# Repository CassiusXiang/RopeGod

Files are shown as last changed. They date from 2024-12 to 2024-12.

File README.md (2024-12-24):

# RopeGod



## Introduction
RopeGod is a highly integrated and low-cost rope-driven five-finger dexterous hand with a total of 7 degrees of freedom.

Each finger segment is equipped with 2 pressure sensors, making a total of 11 force sensors.

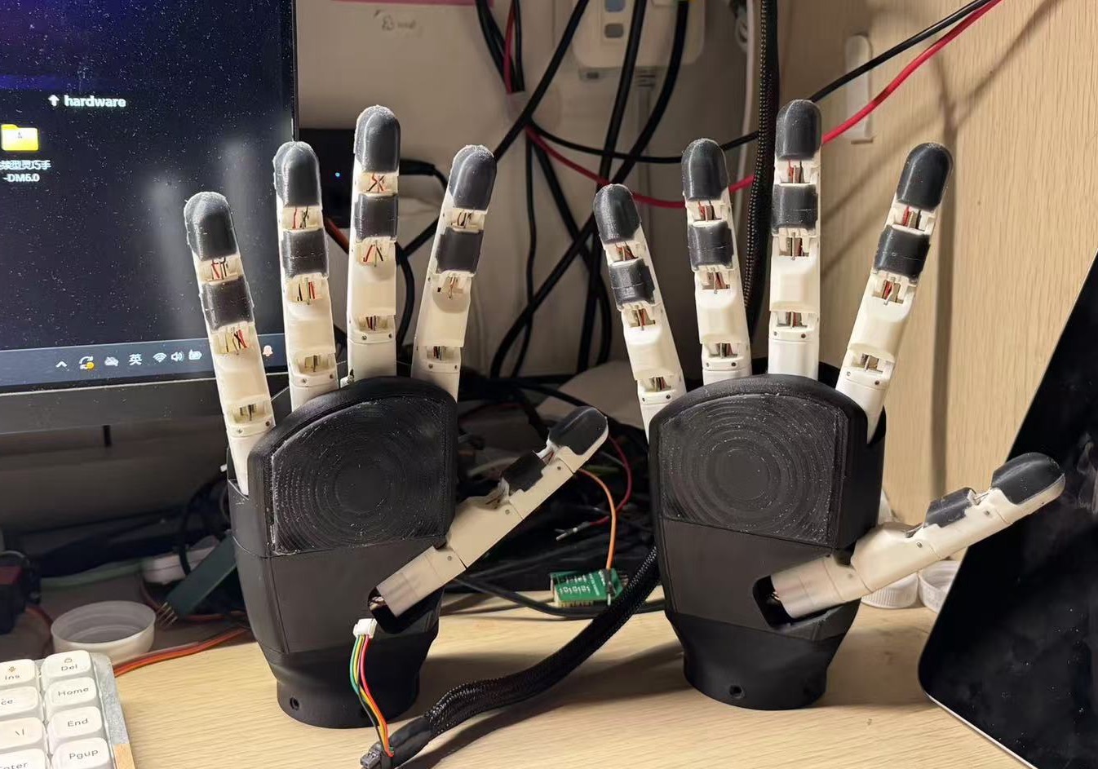
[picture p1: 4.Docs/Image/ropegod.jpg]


## Performance Parameters

| Parameter | Value |
|---|---|
| Weight | 346g |
| Cost | <60$ |
| Number of Sensors | 11 |
| Degrees of Freedom | 7 |
| Maximum Single-Finger Downward Force | 8N |
| Maximum Lifting Weight | 2Kg |
| Power Supply Voltage | 12 ~ 24V |
| Maximum Current | 1.5A |
| Communication | CAN |

## Mechanical Structure

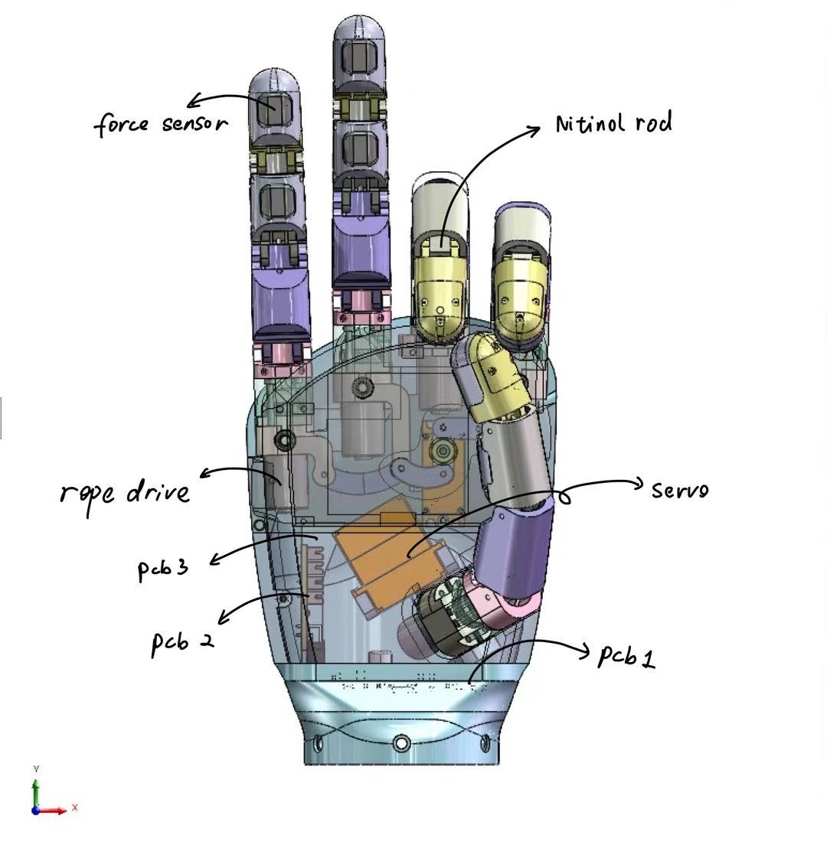
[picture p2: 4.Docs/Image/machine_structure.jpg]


Except for the servos and coreless motors, all other components are independently designed. They can be manufactured via 3D printing, silicone molding with 3D-printed molds, and basic mechanical processing. The models can be found in `/0.Model`.

Currently, our drive structure still involves a single driver board controlling multiple degrees of freedom. Going forward, we are shifting toward a modular design for individual fingers, aiming to integrate drive, control, and current feedback into a single finger, with inter-finger connections using a bus for communication. This will further enhance modular design and reduce space and resource waste.

## Circuit Design

There are three circuit boards inside the palm:
- Motor driver board
- Expansion board (provides driver interfaces)
- Sensor sampling board

This distributed circuit design can further reduce space usage and improve integration. It also offers high flexibility. For example, by changing the sensor board, you can adapt to various sensors (e.g., visual-tactile sensors).

The main control board uses the STM32F103C8T6 for motor control. Each finger’s coreless motor comes with a resistance-based encoder and a closed-loop control board. Therefore, the main controller only needs to supply a stable 12V and an accurate PWM signal to control the rope-driven actuators similarly to controlling servos.

The sensor board uses the STM32F103VET6 as the main controller, primarily because it offers more ADC channels compared to smaller-packaged STM32F1 versions.

Refer to `/1.Hardware` for schematics and PCB designs.

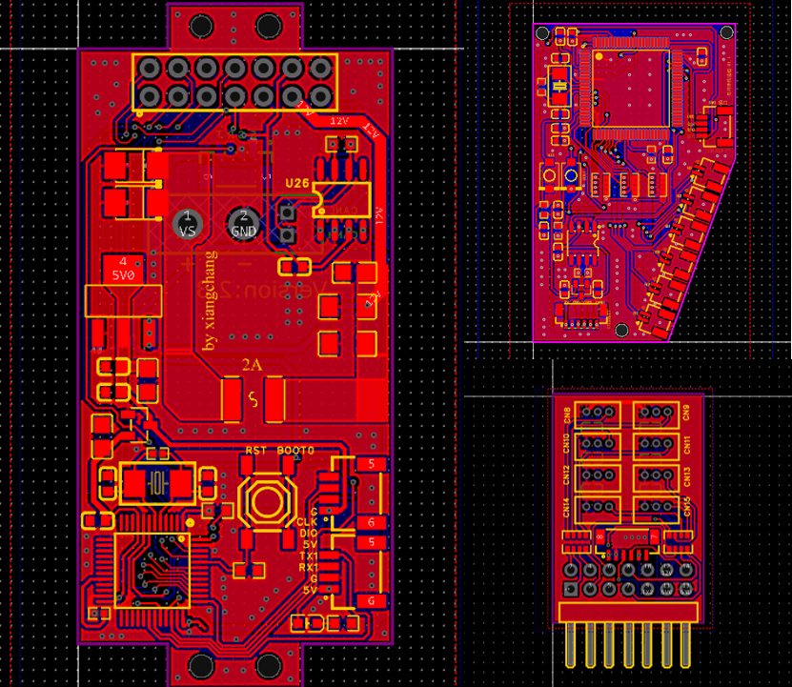
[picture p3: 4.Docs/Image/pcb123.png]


## Firmware

Both the main control board and the sensor board are developed using STM32CubeIDE.

Source code can be found in `2.Firmware`.

## Communication

Since the STM32 series is equipped with a CAN controller peripheral, we only need to add a TJA1042 transceiver. This has already been configured on both the main control board and the sensor board, and both are connected to the CAN network.

For details on the communication protocol, see: [Communication Protocol](./4.Docs/)

## Upper Computer (Host Software)

We use QT to develop a host software application for convenient operation and data collection.

Currently supported features:
1. Closed-loop position control of 7 degrees of freedom
2. Serial connection to a USB-CAN controller
3. Display of joint angle parameters
4. Execution of 4 basic actions (pinch, spherical grasp, lateral pinch, cylindrical grasp)
5. Setting the CAN IDs of the dexterous hand and sensors
6. Chart display of 12 pressure sensor readings

The source code of the upper computer software can be found in `./3.Software`. A pre-compiled version is published in the release section (currently only Windows).

Support for high-resolution screens is not ideal at the moment. We plan to fix this in subsequent releases.

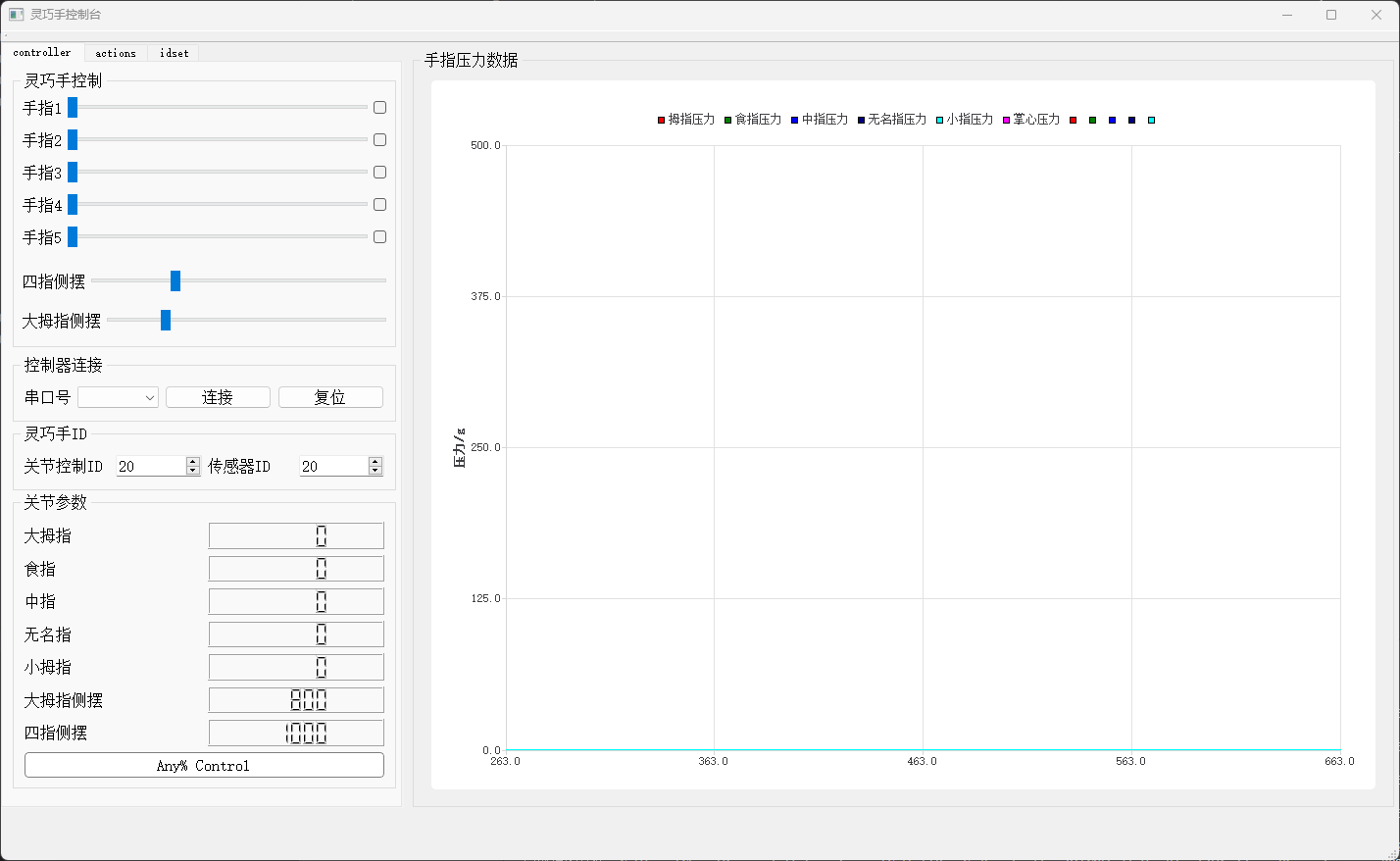
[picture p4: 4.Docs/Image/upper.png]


## Libraries and Interfaces

We provide both C++ and Python library interfaces for convenient secondary development.

See `./3.Software` for details.

Creating a dexterous hand object in C++:
```cpp
WzSerialPort w;
mrh5 mr1(w, 32, 33); 
```

The control frequency should be <200 Hz.

## Video Demonstration
- Degrees of freedom demo: Link 1
- Automatically grasping 9 types of objects and using a barcode scanner to scan barcodes: Link 2
- Using a continuum dexterous hand to grasp fragile items like chips and eggs: Link 3

## Derivative Projects
- Continuum Dexterous Hand
- Metamorphic Dexterous Hand

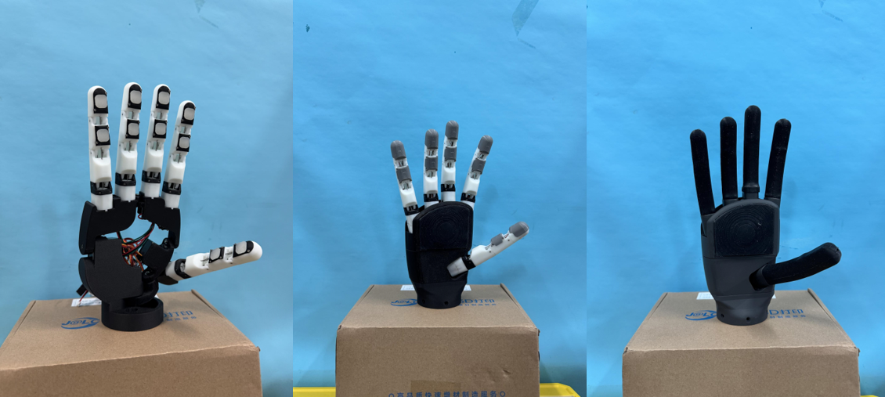
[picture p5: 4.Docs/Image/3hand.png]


## License
Choloepus is released under the AGPL-3.0 License. Please refer to [LICENSE](https://github.com/CassiusXiang/Choloepus/blob/main/LICENSE) for more information.

## Contact
Email: changxiangchina@outlook.com

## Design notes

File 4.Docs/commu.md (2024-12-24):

## Communication Protocol

[go Back](../README.md)

First, connect the USB-CAN module to the computer.

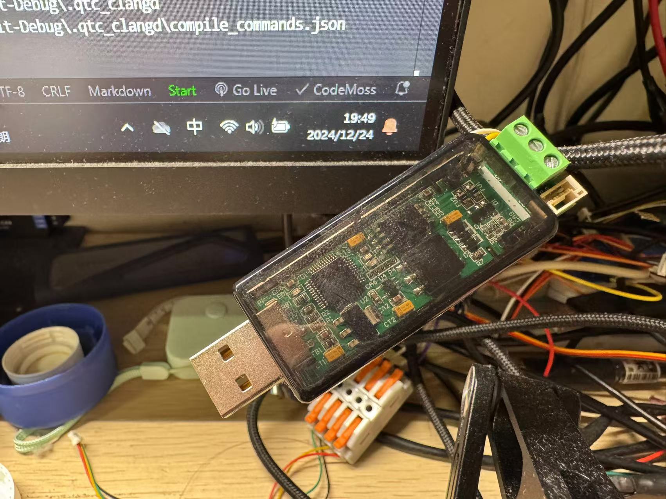
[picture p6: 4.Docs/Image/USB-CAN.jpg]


## Setting Servo Angle

The serial command for setting the servo angle is 16 bytes in length, detailed as follows:

| Command Index | Hex Value |
|---|---|
| 0 | AA |
| 1 | 00 |
| 2 | 00 |
| 3 | 08 |
| 4 | 00 |
| 5 | 00 |
| 6 | High byte of ID |
| 7 | Low byte of ID |
| 8 | 01 |
| 9 | Servo Number |
| 10 | High byte of Angle|
| 11 | Low byte of Angle |
| 12 | 00 |
| 13 | 00 |
| 14 | 00 |
| 15 | 00 |

Angle Correspondence: The physical servo angle ranges from 0 to 180 degrees, corresponding to an electrical servo angle ranging from 0 to 2000.

## Pressure Reading

The pressure data format returned by the sensor is as follows:

The sensor ID is calculated as 2047 minus the set sensor ID (default is 33).

| Command Index | Hex Value |
|---|---|
| 0 | AA |
| 1 | 00 |
| 2 | 00 |
| 3 | 08 |
| 4 | 00 |
| 5 | 00 |
| 6 | High byte of ID |
| 7 | Low byte of ID |
| 8 | Pressure Sensor Number |
| 9 | High byte of Pressure Data |
| 10 | Low byte of Pressure Data  |
| 11 | 00 |
| 12 | 00 |
| 13 | 00 |
| 14 | 00 |
| 15 | 00 |

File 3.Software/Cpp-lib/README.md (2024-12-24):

# MRH5 灵巧手C++库

本项目适用于Windows平台

在根目录下，运行：

```\
make
```

即可生成可执行文件

如果您未经设置可能不能直接使用make，可以用如下命令代替

```
mingw32-make.exe
```

## 备注

- 在Windows上，要打开COM10以后的串口（包括COM10），串口名称不再是“COM10”，而是“\\.\COM10”，因此在open函数中，如果是COM10及以后的串口，串口名（假设当前要打开COM10）应该写“\\\\.\\COM10”，其中“\\\\.\\”为“\\.\”的转义。

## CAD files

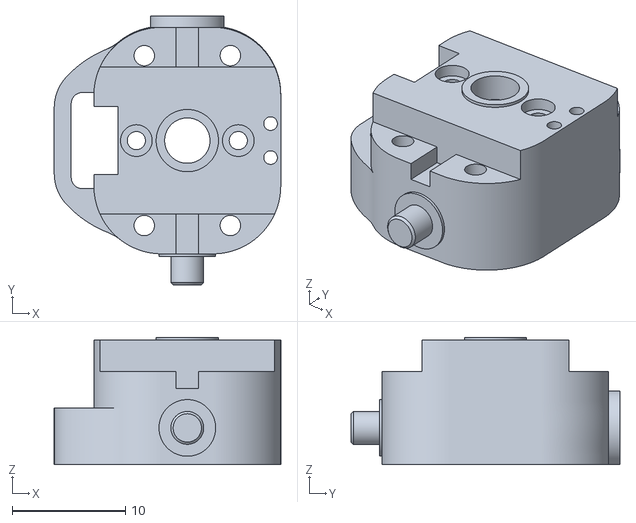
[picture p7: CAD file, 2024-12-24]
0.Model/三维猴打印/拇指机架_L.STL
20.0 x 23.8 x 11.2

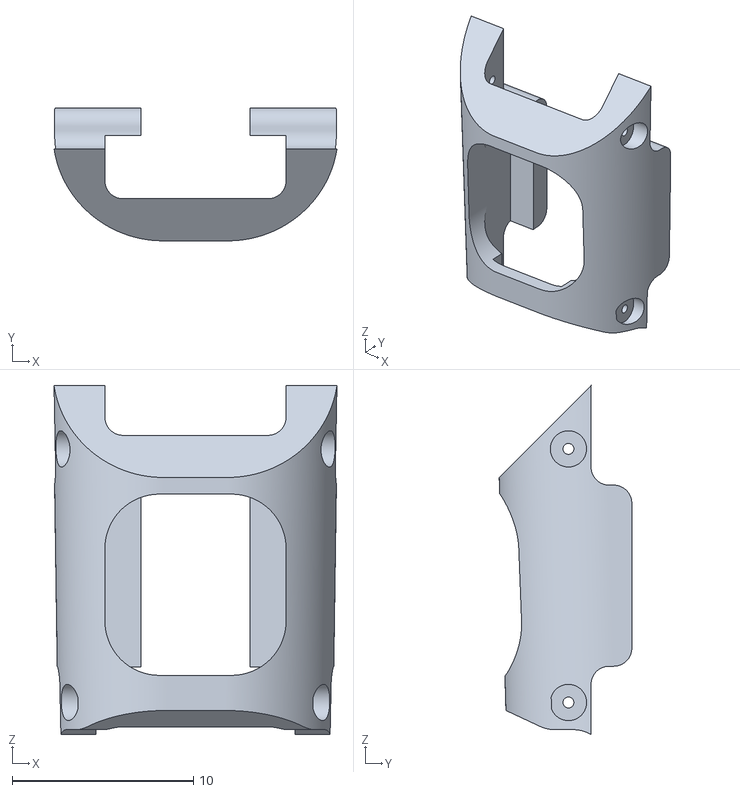
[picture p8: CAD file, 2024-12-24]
0.Model/中指/中端 - 盖.STL
15.6 x 7.32 x 19.3

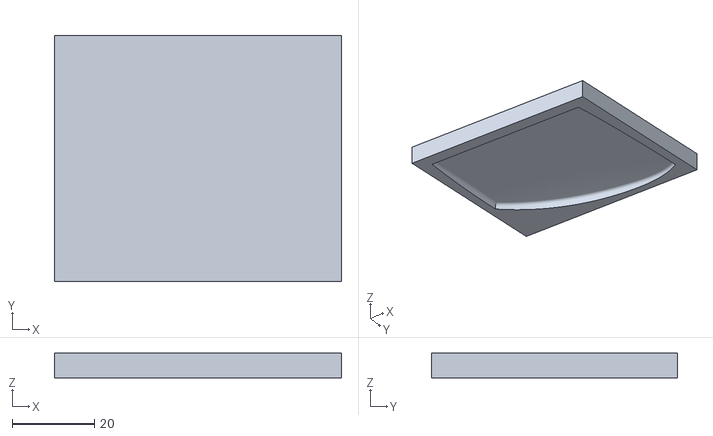
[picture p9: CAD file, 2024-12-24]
0.Model/手掌硅胶壳右1.STL
70.0 x 60.0 x 6.00

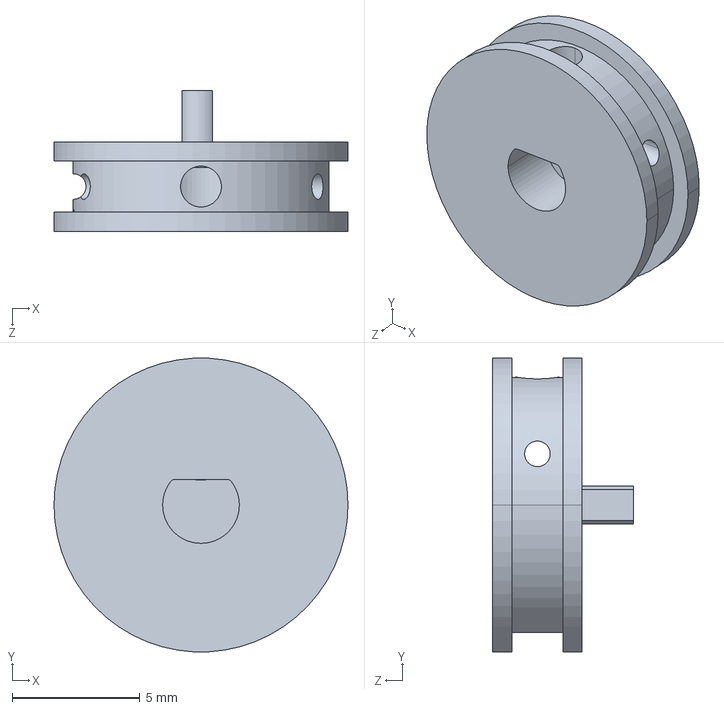
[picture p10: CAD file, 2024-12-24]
0.Model/拇指/绕线盘.STEP
11.5 x 11.5 x 5.50 mm

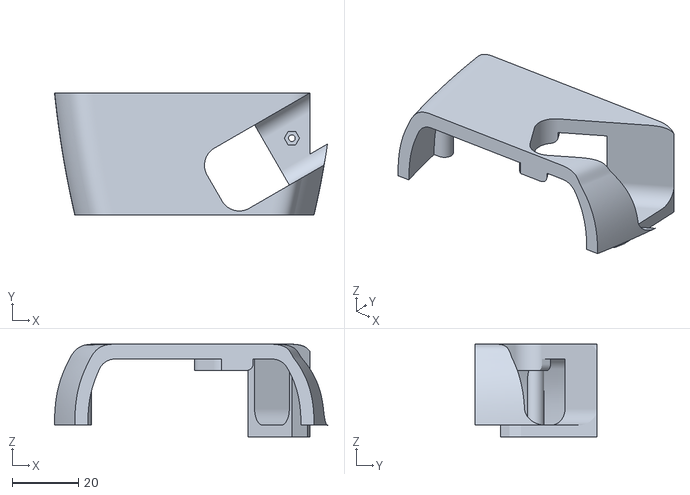
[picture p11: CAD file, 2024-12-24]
0.Model/三维猴打印/手掌盖.STL
82.5 x 36.9 x 28.0

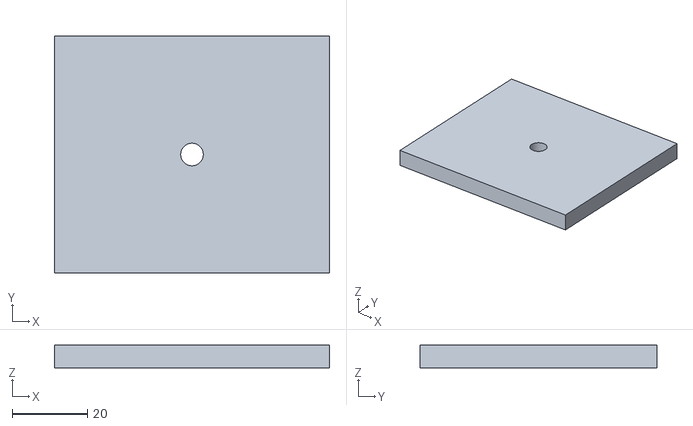
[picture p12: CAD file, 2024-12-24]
0.Model/手掌硅胶壳左2.STL
73.0 x 63.0 x 6.00

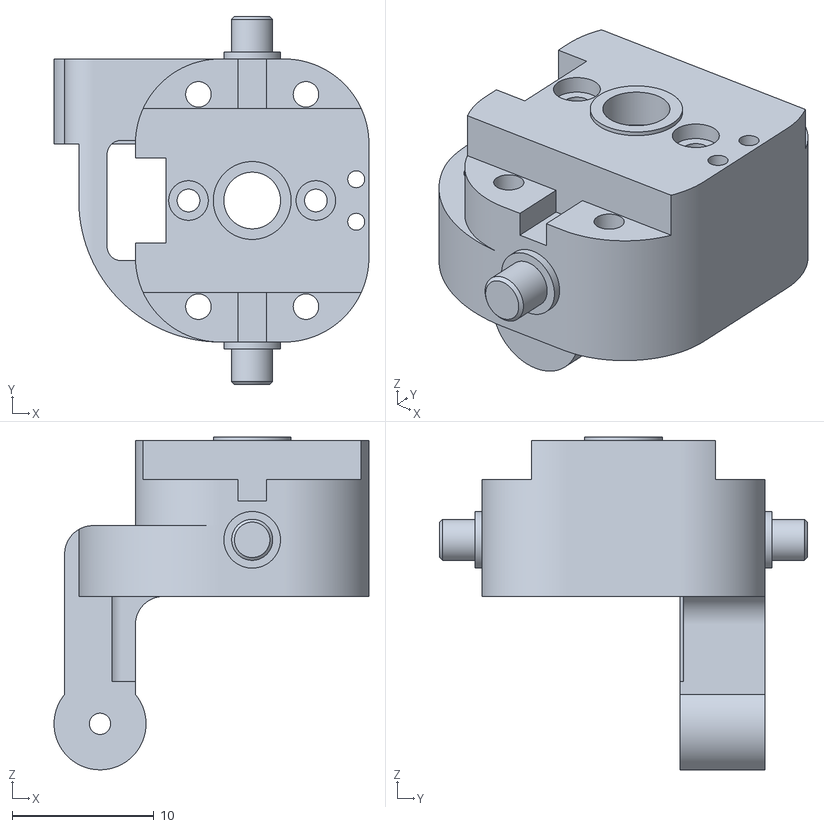
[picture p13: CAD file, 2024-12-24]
0.Model/未来工厂打印/食指机架_L.STL
22.2 x 26.0 x 23.5

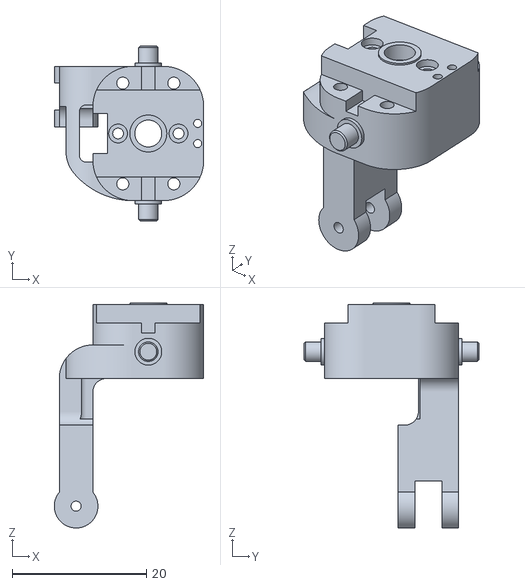
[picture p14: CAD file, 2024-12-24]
0.Model/三维猴打印/无名指机架.STL
22.2 x 26.0 x 33.5

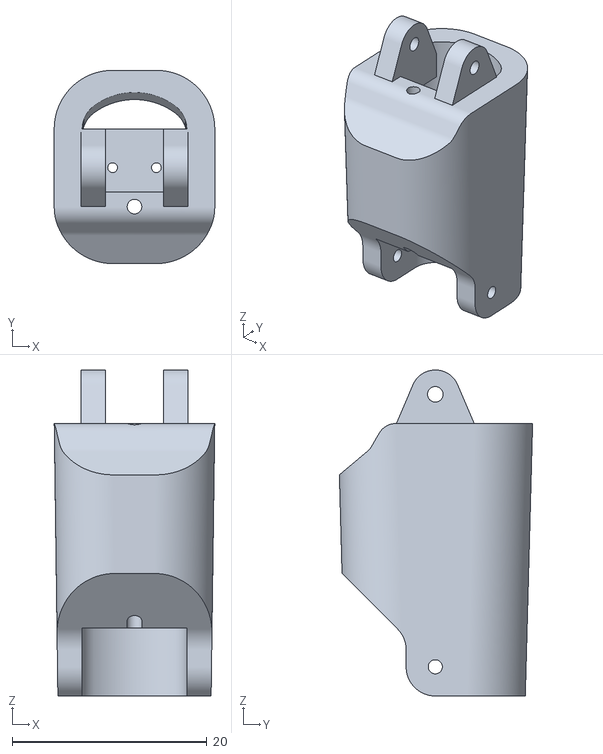
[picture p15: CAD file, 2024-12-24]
0.Model/三维猴打印/近端.STL
16.5 x 19.9 x 33.5

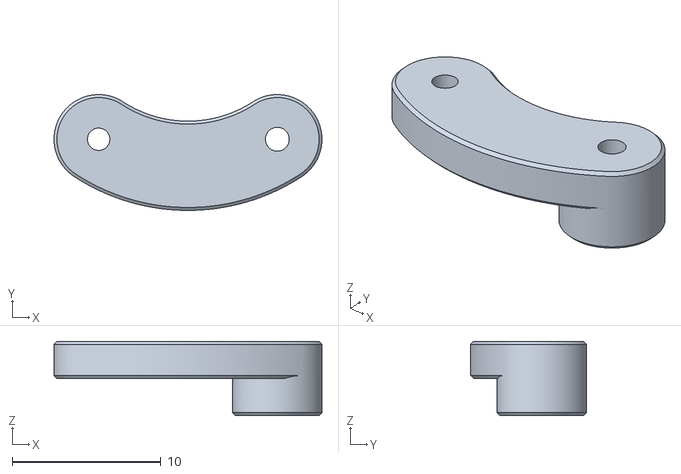
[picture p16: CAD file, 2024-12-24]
0.Model/未来工厂打印/连杆3_L.STL
18.0 x 7.78 x 5.00

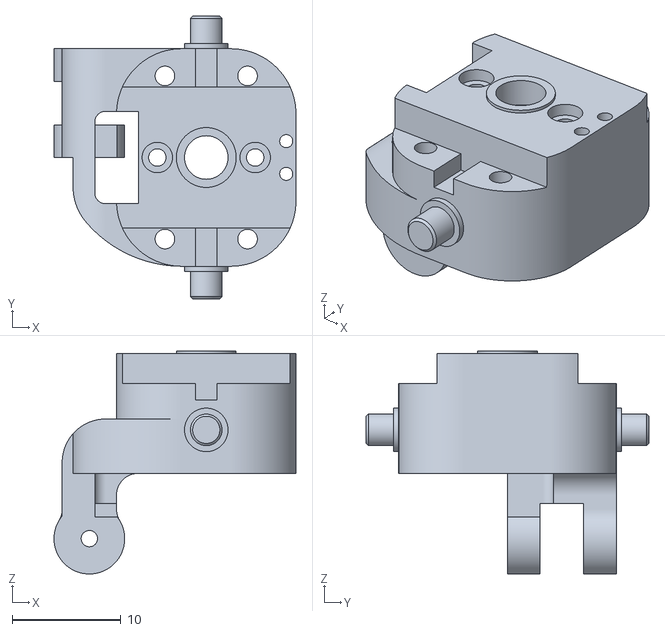
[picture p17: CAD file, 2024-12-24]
0.Model/三维猴打印/小指机架.STL
22.2 x 26.0 x 20.5

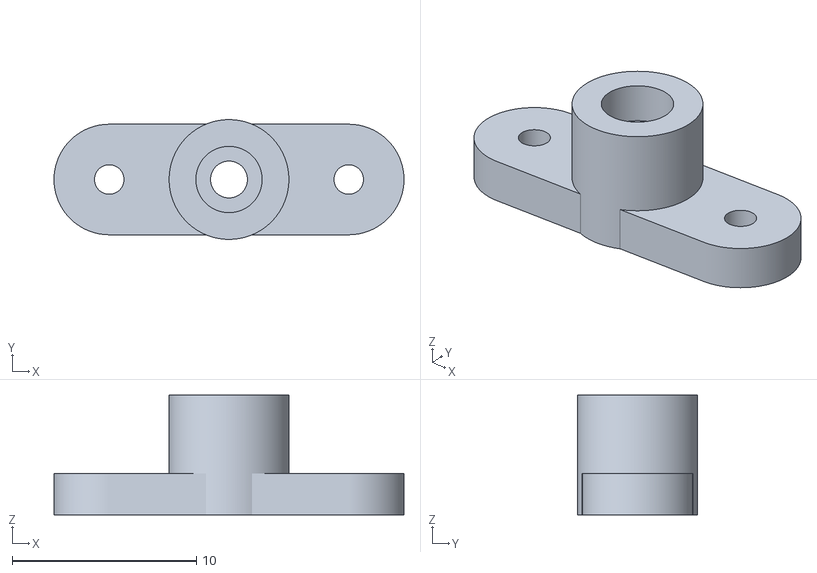
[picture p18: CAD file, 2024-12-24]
0.Model/未来工厂打印/连杆2.STL
19.0 x 6.50 x 6.50

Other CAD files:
0.Model/未来工厂打印/拇指机架.STL
0.Model/手掌硅胶壳左1.STL
0.Model/未来工厂打印/食指机架.STL
0.Model/手掌硅胶壳右2.STL
0.Model/未来工厂打印/无名指机架_L.STL
0.Model/三维猴打印/无名指机架_L.STL
0.Model/三维猴打印/中指机架.STL
0.Model/三维猴打印/中指机架_L.STL
0.Model/三维猴打印/中端.STL
0.Model/三维猴打印/小指机架_L.STL
0.Model/三维猴打印/手指基座.STL
0.Model/三维猴打印/拇指机架.STL
0.Model/三维猴打印/拇指电机机架.STL
0.Model/三维猴打印/拇指电机机架_L.STL
0.Model/三维猴打印/食指机架.STL
0.Model/中指/makeProjectedPlanarWire.x_t
0.Model/未来工厂打印/中指机架.STL
0.Model/未来工厂打印/中指机架_L.STL
0.Model/未来工厂打印/小指机架_L.STL
0.Model/未来工厂打印/手掌盖_L.STL
0.Model/未来工厂打印/拇指电机机架.STL
0.Model/未来工厂打印/拇指电机机架_L.STL
0.Model/未来工厂打印/连杆1.STL
0.Model/未来工厂打印/连杆1_L.STL
0.Model/未来工厂打印/连杆3.STL
0.Model/未来工厂打印/连杆4.STL

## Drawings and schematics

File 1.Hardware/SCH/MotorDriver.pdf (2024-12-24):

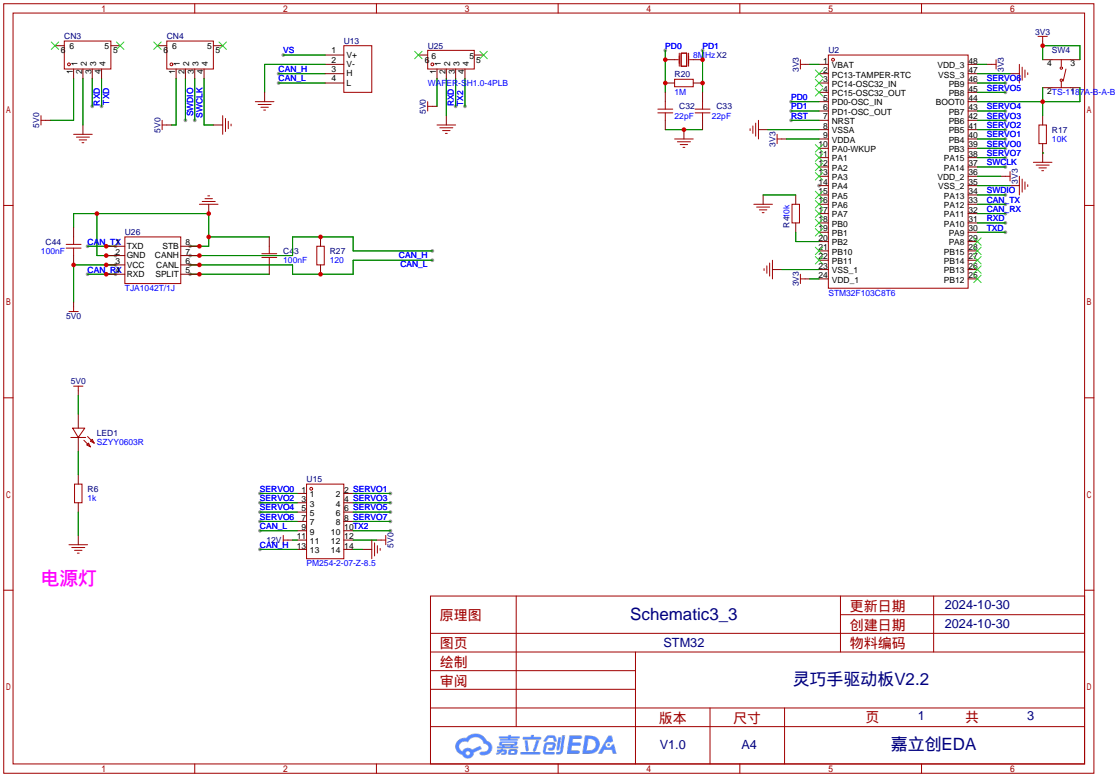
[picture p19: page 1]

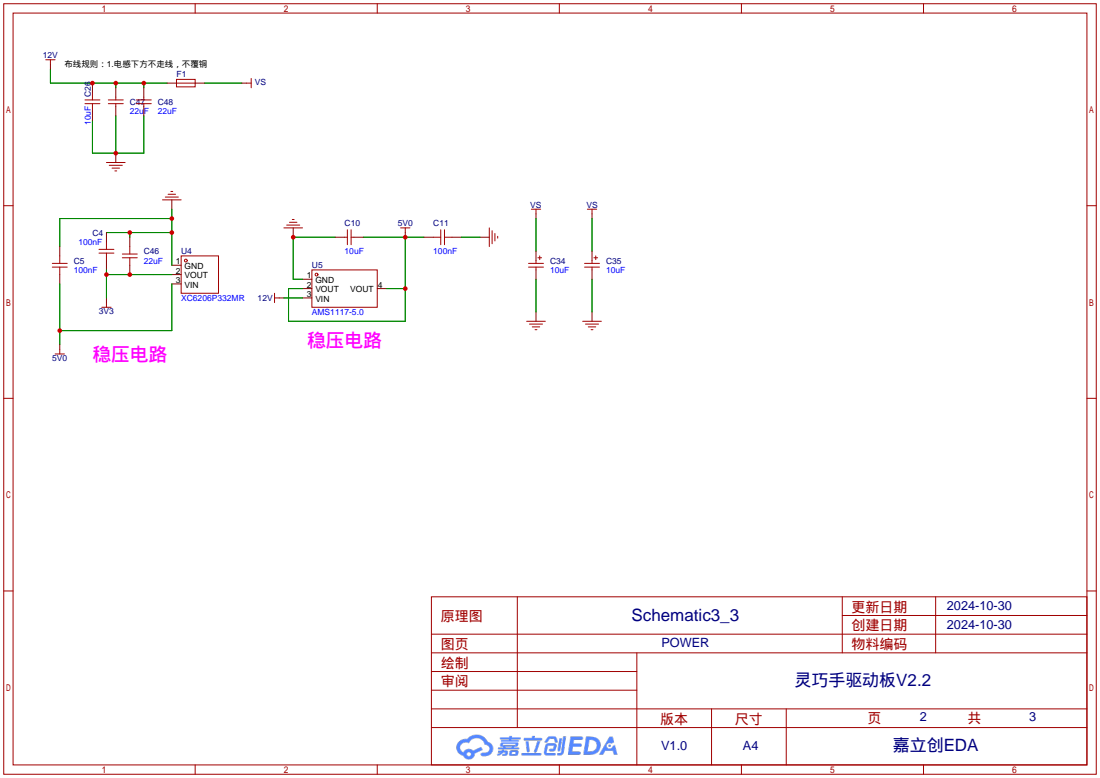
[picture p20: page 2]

审阅

绘制

### 创建日期 物料编码 页

共

原理图 | 更新日期

图页

| 灵巧手驱动板V2.2

2024-10-30
2024-10-30 Schematic3_3 | 3

P3

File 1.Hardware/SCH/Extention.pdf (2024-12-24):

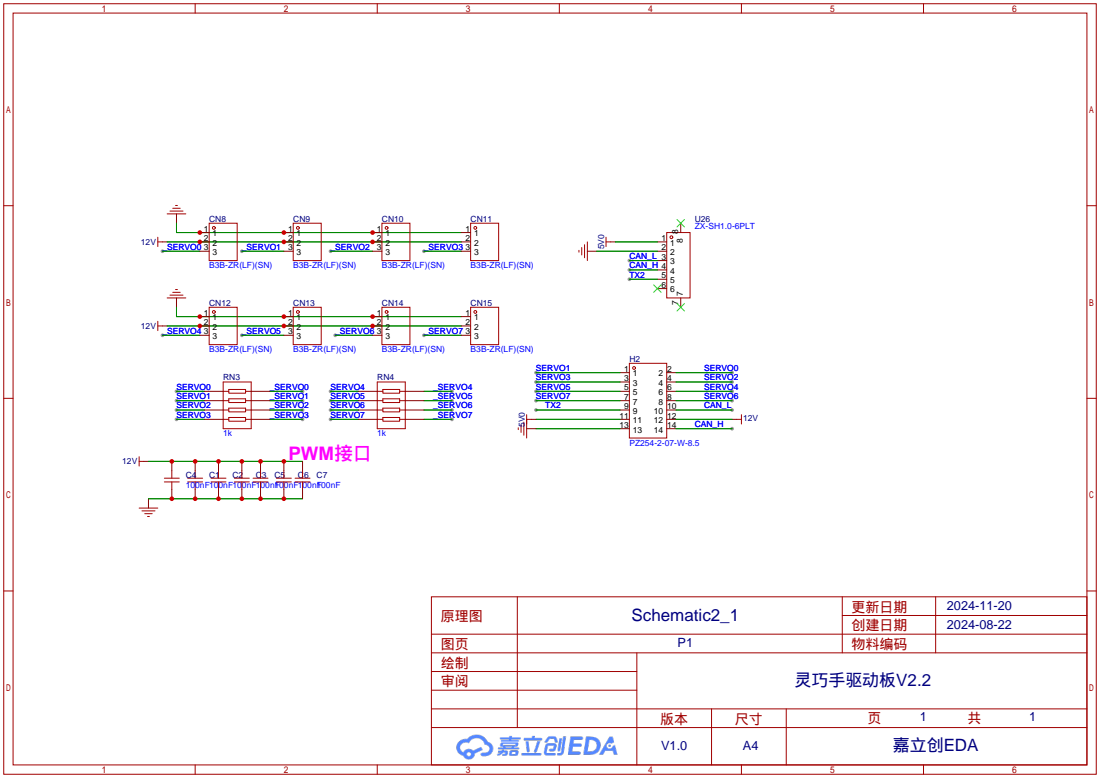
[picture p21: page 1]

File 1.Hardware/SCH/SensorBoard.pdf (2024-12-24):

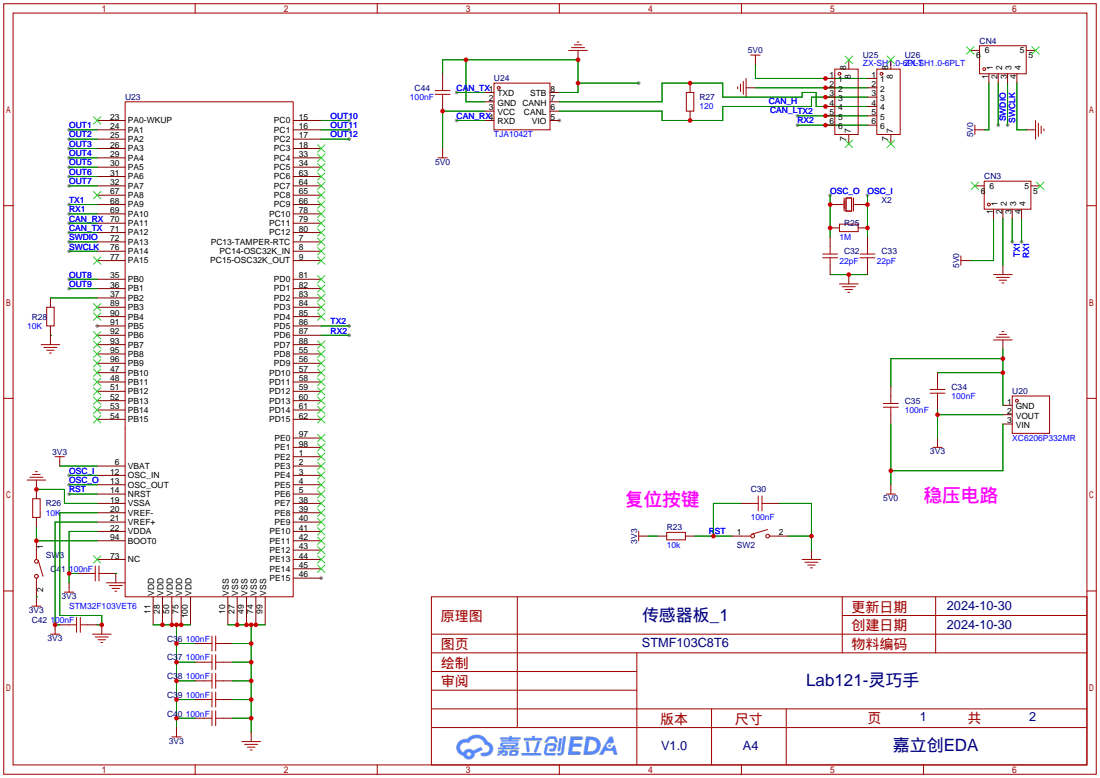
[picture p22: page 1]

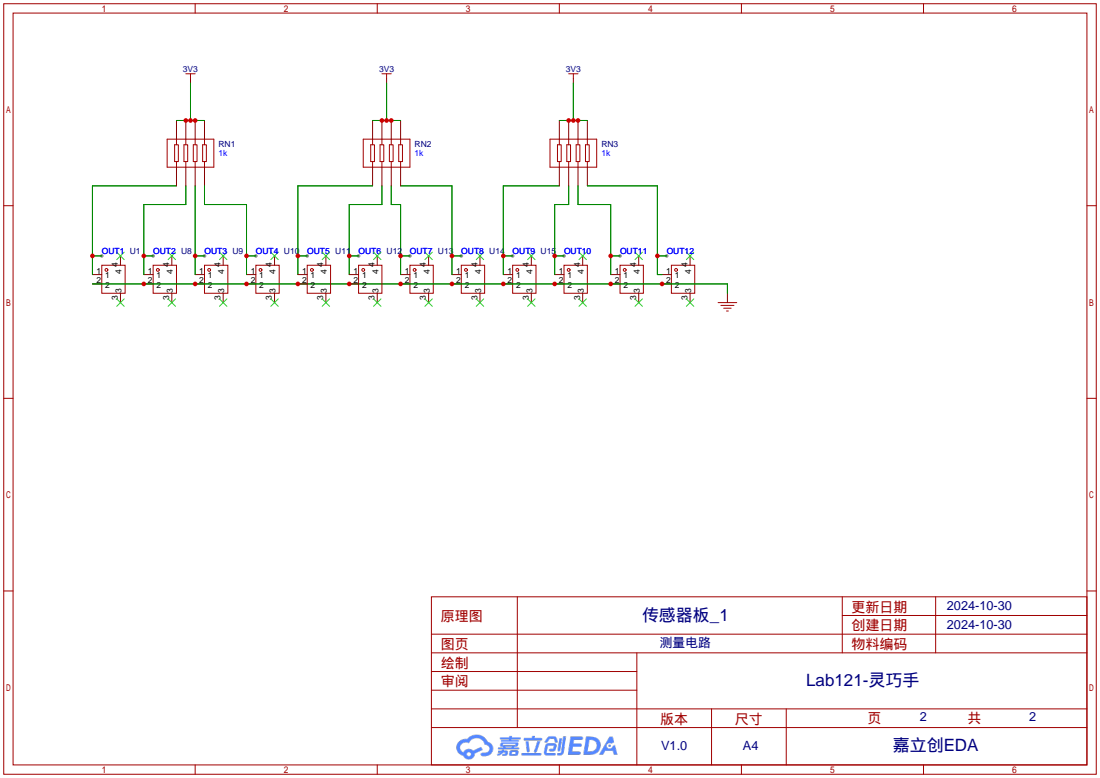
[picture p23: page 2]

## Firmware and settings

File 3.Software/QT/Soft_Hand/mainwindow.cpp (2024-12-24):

#include "mainwindow.h"
#include "ui_mainwindow.h"

MainWindow::MainWindow(QWidget *parent) :
    QMainWindow(parent),
    ui(new Ui::MainWindow)
{
    ui->setupUi(this);
    this->setWindowTitle("灵巧手控制台");
//    QImage demoHand("./fig/demo.png");
//    QPixmap pixmap = QPixmap::fromImage(demoHand);
//    ui->display->setPixmap(pixmap);

    serialportscan();
    comflag = 0;
    idsetflag = 0;
    for(int i = 0; i < 8; i++){
        servo_angle[i] = 500;
    }
    for(int i = 0; i < 12; i++){
        pressure[i] = 0;
    }
    for(int i = 0; i < 4; i++){
        pressureMotion[i] = 0;
    }
//    uint8_t pressure_it = 1;
    time_tick = 0;
    xrange = 400;
    uint8_t its = 0;
    uint8_t itp = 0;
    charinit();

    QPushButton *button3 = ui->pushButton_3;
    QPushButton *button4 = ui->pushButton_4;
    QPushButton *button5 = ui->pushButton_5;
    QPushButton *button12 = ui->pushButton_12;
    QPushButton *button7 = ui->pushButton_7;

    QProgressBar *bar3 = ui->progressBar_3;
    QProgressBar *bar4 = ui->progressBar_10;

    // 创建按钮组并设置互斥
    QButtonGroup *buttonGroup = new QButtonGroup(this);
    buttonGroup->setExclusive(true);

    // 设置按钮为可切换状态（checkable）
    button3->setCheckable(true);
    button4->setCheckable(true);
    button5->setCheckable(true);
    button12->setCheckable(true);
    button7->setCheckable(true);

    // 添加按钮到组
    buttonGroup->addButton(button3);
    buttonGroup->addButton(button4);
    buttonGroup->addButton(button5);
    buttonGroup->addButton(button12);
    buttonGroup->addButton(button7);

    // 设置按钮的样式表（QSS）
    // 未按下时是默认颜色，按下时背景变为绿色
    QString buttonStyle = R"(
        QPushButton {
            background-color: white;
            border: 1px solid gray;
            border-radius: 4px;
            padding: 4px;
        }
        QPushButton:checked {
            background-color: #CCFFCC; /* 淡绿色 */
            color: black;
        }
    )";
    button3->setStyleSheet(buttonStyle);
    button4->setStyleSheet(buttonStyle);
    button5->setStyleSheet(buttonStyle);
    button12->setStyleSheet(buttonStyle);
    button7->setStyleSheet(buttonStyle);


    ui->finger1->setRange(0, 2000);
    ui->finger1->setValue(0);
    ui->finger2->setRange(0, 2000);
    ui->finger2->setValue(0);
    ui->finger3->setRange(0, 2000);
    ui->finger3->setValue(0);
    ui->finger4->setRange(0, 2000);
    ui->finger4->setValue(0);
    ui->finger5->setRange(0, 2000);
    ui->finger5->setValue(0);

    ui->damuzhi->setRange(600, 1600);
    ui->damuzhi->setValue(800);
    ui->sizhi->setRange(900, 1260);
    ui->sizhi->setValue(1000);

    ui->spinBox->setValue(20);
    ui->spinBox_2->setValue(20);
    ui->spinBox->setRange(20, 65535);
    ui->spinBox_2->setRange(20, 65535);

    ui->finger2catch->setRange(0, 1000);
    ui->finger2catch_2->setRange(0, 1000);
    ui->finger2catch_3->setRange(0, 2000);
    ui->finger2catch_10->setRange(0, 1000);
    ui->finger2catch_11->setRange(0, 1000);

    bar3->setValue(0);
    bar4->setValue(0);




    connect(ui->pushButton, &QPushButton::clicked, this, &MainWindow::serialopen);
    connect(ui->pushButton_2, &QPushButton::clicked, this, &MainWindow::reset);
//    connect(ui->pushButton_3, &QPushButton::clicked, this, &MainWindow::setcanid);
    connect(ui->pushButton_6, &QPushButton::clicked, this, &MainWindow::setid);
    connect(&timer_1, &QTimer::timeout, [&](){
        // When timer timeout
        servo_angle[0] = static_cast<uint16_t>(ui->sizhi->value());
        servo_angle[1] = static_cast<uint16_t>(ui->damuzhi->value());
        servo_angle[2] = static_cast<uint16_t>(ui->finger1->value());
        servo_angle[3] = static_cast<uint16_t>(ui->finger2->value());
        servo_angle[4] = static_cast<uint16_t>(ui->finger3->value());
        servo_angle[5] = static_cast<uint16_t>(ui->finger4->value());
        servo_angle[6] = static_cast<uint16_t>(ui->finger5->value());

//        for(uint8_t i = 0; i < 7; i++){
        if(idsetflag){
            setcanid();
            idsetflag = 0;
        }
        else{
            ControlAngle(its, servo_angle[its]);
        }
//        }
//        for(uint8_t i = 0; i < 6; i++){
//            GetPressure(itp);
//        }
            its = (its + 1)%7;
            itp = (itp + 1)%6;
    });

    connect(&timer_plot, &QTimer::timeout, [&](){
        // When timer timeout
        charpointupdate();

        ui->lcdNumber_11->display(ui->finger1->value());
        ui->lcdNumber_12->display(ui->finger2->value());
        ui->lcdNumber_13->display(ui->finger3->value());
        ui->lcdNumber_14->display(ui->finger4->value());
        ui->lcdNumber_15->display(ui->finger5->value());
        ui->lcdNumber_16->display(ui->damuzhi->value());
        ui->lcdNumber_17->display(ui->sizhi->value());


        pressureMotion[0] = pressure[0] + pressure[1];
        pressureMotion[1] = pressure[1] + pressure[2];
        pressureMotion[2] = pressure[0] + pressure[1] + pressure[2] + pressure[3] + pressure[4];
        pressureMotion[3] = pressure[0] + pressure[1] + pressure[2] + pressure[3] + pressure[4];

        ui->lcdNumber->display(pressureMotion[0]);
        ui->lcdNumber_2->display(pressureMotion[1]);
        ui->lcdNumber_3->display(pressureMotion[2]);





        if(ui->pushButton_3->isChecked()){
            ui->damuzhi->setValue(1093);
            int target = ui->finger2catch->value();
            ui->finger1->setValue(static_cast<int>(target*0.618));
            ui->finger2->setValue(static_cast<int>(target*1.481));
        } else if(ui->pushButton_4->isChecked()){
            int target2 = ui->finger2catch_2->value();
            ui->finger2->setValue(359);
            ui->finger3->setValue(353);
            ui->sizhi->setValue(800 + static_cast<int>(target2*0.46));
        } else if(ui->pushButton_5->isChecked()){
            int target3 = ui->finger2catch_3->value();
            int successp = pressureMotion[2]/6;
            ui->finger1->setValue(target3);
            ui->finger2->setValue(target3);
            ui->finger3->setValue(target3);
            ui->finger4->setValue(target3);
            ui->finger5->setValue(target3);
            if(successp > 100){
                successp = 100;
            }
            ui->progressBar_3->setValue(successp);
        } else if(ui->pushButton_12->isChecked()){
            int target4 = ui->finger2catch_10->value();
            int target5 = ui->finger2catch_11->value();
            ui->sizhi->setValue(1116);
            ui->damuzhi->setValue(1330);
            ui->finger1->setValue(static_cast<int>(target4*0.800));
            ui->finger2->setValue(static_cast<int>(target5*2));
            ui->finger3->setValue(static_cast<int>(target4*0.324));
            ui->finger4->setValue(static_cast<int>(target4*1.982));
            ui->finger5->setValue(static_cast<int>(target4*1.982));
        }

    });

    // Connect sliderMoved signals to update other sliders when synced
    connect(ui->finger1, &QSlider::sliderMoved, this, &MainWindow::onSliderMoved);
    connect(ui->finger2, &QSlider::sliderMoved, this, &MainWindow::onSliderMoved);
    connect(ui->finger3, &QSlider::sliderMoved, this, &MainWindow::onSliderMoved);
    connect(ui->finger4, &QSlider::sliderMoved, this, &MainWindow::onSliderMoved);
    connect(ui->finger5, &QSlider::sliderMoved, this, &MainWindow::onSliderMoved);
}

MainWindow::~MainWindow()
{
    delete ui;
}

void MainWindow::serialportscan(){
    foreach(const QSerialPortInfo &info, QSerialPortInfo::availablePorts()){
        QSerialPort ser;
        ser.setPort(info);
        if(ser.open(QIODevice::ReadWrite)){
            ui->comboBox->addItem(ser.portName());
            ser.close();
        }
    }
}

bool MainWindow::serialopen(){ // Yellow:GND. Black:RX. Red:TX
    serial = new QSerialPort;
    serial->setPortName(ui->comboBox->currentText());
    serial->setBaudRate(QSerialPort::Baud115200);
    serial->setDataBits(QSerialPort::Data8);
    serial->setParity(QSerialPort::NoParity);
    serial->setStopBits(QSerialPort::OneStop);
    serial->setFlowControl(QSerialPort::NoFlowControl);
    serial->open(QIODevice::ReadWrite);
    if(serial->isOpen()){
//        QMessageBox::about(this, tr("串口连接"), tr("连接成功"));
        ui->pushButton->setText("已连接");
        comflag = 1;
        connect(serial, &QSerialPort::readyRead, this, &MainWindow::SerialReciveMsg);
//        ControlAngle(1, 500);
        return true;
    }
    else {
        return false;
    }
}

void MainWindow::SerialReciveMsg(){
    QByteArray buf = serial->readAll();
    serialBuffer.append(buf);

    while (serialBuffer.size() >= 16) { // 当缓冲区中至少有一个完整的数据帧
        // 查找帧的起始位置（0xAA）
        int startIndex = serialBuffer.indexOf(static_cast<char>(0xAA));
        if (startIndex == -1) {
            // 如果没有找到起始标识，清空缓冲区
            serialBuffer.clear();
//            qDebug() << "Error: No start byte (0xAA) found. Buffer cleared.";
            return;
        }

        // 如果起始标识不是在第一个位置，移除之前的数据
        if (startIndex > 0) {
            serialBuffer.remove(0, startIndex);
//            qDebug() << "Info: Discarding" << startIndex << "bytes before start byte (0xAA).";
        }

        // 检查缓冲区中是否有足够的数据帧
        if (serialBuffer.size() < 16) {
            // 数据不完整，等待下次接收
            return;
        }

        // 检查第16字节是否为结束标识0x00
        if (static_cast<uint8_t>(serialBuffer.at(15)) != 0x00) {
//            qDebug() << "Error: Frame does not end with 0x00. Discarding first byte.";
            serialBuffer.remove(0, 1); // 移除第一个字节，重新寻找起始字节
            continue;
        }

        // 提取一个完整的数据帧
        QByteArray frame = serialBuffer.left(16);
        serialBuffer.remove(0, 16); // 移除已处理的帧

        // 解析数据帧
        QVector<uint8_t> hexValues;
        for (int i = 0; i < frame.size(); ++i) {
            hexValues.append(static_cast<uint8_t>(frame.at(i)));
        }

        // 打印接收到的数据帧（十六进制）
        QString hexString;
        for (uint8_t val : hexValues) {
            hexString.append(QString::number(val, 16).rightJustified(2, '0').toUpper() + " ");
        }
//        qDebug() << "Received hex values:" << hexString.trimmed();

        // 解析 ID 和压力值
        uint16_t reciveId = static_cast<uint16_t>((hexValues[6] << 8) + hexValues[7]);
        uint16_t compareId = 2047 - static_cast<uint16_t>(ui->spinBox_2->value()); // 压力消息帧的 ID

        // 校验帧头、帧类型和 ID
        if (hexValues[0] == 0xAA && hexValues[3] == 0x08 && reciveId == compareId) {
            uint8_t pressureId = hexValues[8];
            if (pressureId >= 12) { // 确保 pressureId 不超过数组范围
//                qDebug() << "Error: Invalid pressureId" << pressureId;
                continue;
            }
            uint16_t pressureValue = static_cast<uint16_t>((hexValues[9] << 8) + hexValues[10]);
            pressure[pressureId] = 4000000/(pressureValue + 1) - 1000;
//            pressure[pressureId] = pressureValue;
//            qDebug() << "Pressure ID:" << pressureId << "Value:" << pressureValue;
        }
        else {
//            qDebug() << "Error: Invalid frame format or ID mismatch.";
        }
    }
}

void MainWindow::ControlAngle(uint8_t id, uint16_t angle){
    uint8_t data[16];
    uint16_t boardId = static_cast<uint16_t>(ui->spinBox->value());
    if(comflag){
        data[0] = 0xAA;
        data[1] = 0x00;
        data[2] = 0x00;
        data[3] = 0x08;

        data[4] = 0x00;
        data[5] = 0x00;
        data[6] = (boardId >> 8);
        data[7] = boardId & 0xFF;

        data[8] = 0x01;
        data[9] = id & 0xFF;
        data[10] = (angle >> 8);
        data[11] = angle & 0xFF;

        data[12] = 0x00;
        data[13] = 0x00;
        data[14] = 0x00;
        data[15] = 0x00;
//        QByteArray byteArray(reinterpret_cast<const char*>(data), sizeof(data));
//        qDebug() << "Data array (hex):" << byteArray.toHex(' ');
        serial->write(reinterpret_cast<char*>(data), sizeof(data));
    }
}

void MainWindow::GetPressure(uint8_t id){
    uint8_t data[16];
    uint16_t boardId = static_cast<uint16_t>(ui->spinBox_2->value());
//    uint16_t pressureId = 65535 - boardId;
    if(comflag){
        data[0] = 0xAA;
        data[1] = 0x00;
        data[2] = 0x00;
        data[3] = 0x08;

        data[4] = 0x00;
        data[5] = 0x00;
        data[6] = (boardId >> 8);
        data[7] = boardId & 0xFF;

        data[8] = 0x01;
        data[9] = id & 0xFF;
        data[10] = 0x00;
        data[11] = 0x00;

        data[12] = 0x00;
        data[13] = 0x00;
        data[14] = 0x00;
        data[15] = 0x00;
        serial->write(reinterpret_cast<char*>(data), sizeof(data));
    }
}

void MainWindow::charinit(){
    MyChartViewFinger1 = ui->chart;
    MyChartViewFinger1->setChart(&MyChartFinger1);
    pressure1 = new QSplineSeries(this);
    pressure2 = new QSplineSeries(this);
    pressure3 = new QSplineSeries(this);
    pressure4 = new QSplineSeries(this);
    pressure5 = new QSplineSeries(this);
    pressure6 = new QSplineSeries(this);
    pressure7 = new QSplineSeries(this);
    pressure8 = new QSplineSeries(this);
    pressure9 = new QSplineSeries(this);
    pressure10 = new QSplineSeries(this);
    pressure11 = new QSplineSeries(this);
    pressure12 = new QSplineSeries(this);

    MyChartFinger1.addSeries(pressure1);
    MyChartFinger1.addSeries(pressure2);
    MyChartFinger1.addSeries(pressure3);
    MyChartFinger1.addSeries(pressure4);
    MyChartFinger1.addSeries(pressure5);
    MyChartFinger1.addSeries(pressure6);
    MyChartFinger1.addSeries(pressure7);
    MyChartFinger1.addSeries(pressure8);
    MyChartFinger1.addSeries(pressure9);
    MyChartFinger1.addSeries(pressure10);
    MyChartFinger1.addSeries(pressure11);

    pressure1->setName("拇指压力");
    pressure2->setName("食指压力");
    pressure3->setName("中指压力");
    pressure4->setName("无名指压力");
    pressure5->setName("小指压力");
    pressure6->setName("掌心压力");
//    pressure7->setName("拇指肚压力");
//    pressure8->setName("食指肚压力");
//    pressure9->setName("中指肚压力");
//    pressure10->setName("无名指肚压力");
//    pressure11->setName("小指肚压力");

    MyChartFinger1.addAxis(&pressure1X, Qt::AlignBottom);
    MyChartFinger1.addAxis(&pressure1Y, Qt::AlignLeft);

    pressure1Y.setTitleText("压力/g");
    pressure1Y.setRange(0, 500);
    pressure1X.setRange(0, xrange);

    pressure1->attachAxis(&pressure1X);
    pressure1->attachAxis(&pressure1Y);
    pressure2->attachAxis(&pressure1X);
    pressure2->attachAxis(&pressure1Y);
    pressure3->attachAxis(&pressure1X);
    pressure3->attachAxis(&pressure1Y);
    pressure4->attachAxis(&pressure1X);
    pressure4->attachAxis(&pressure1Y);
    pressure5->attachAxis(&pressure1X);
    pressure5->attachAxis(&pressure1Y);
    pressure6->attachAxis(&pressure1X);
    pressure6->attachAxis(&pressure1Y);
    pressure7->attachAxis(&pressure1X);
    pressure7->attachAxis(&pressure1Y);
    pressure8->attachAxis(&pressure1X);
    pressure8->attachAxis(&pressure1Y);
    pressure9->attachAxis(&pressure1X);
    pressure9->attachAxis(&pressure1Y);
    pressure10->attachAxis(&pressure1X);
    pressure10->attachAxis(&pressure1Y);
    pressure11->attachAxis(&pressure1X);
    pressure11->attachAxis(&pressure1Y);

    pressure1->setColor(Qt::red);
    pressure7->setColor(Qt::red);
    pressure2->setColor(Qt::darkGreen);
    pressure8->setColor(Qt::darkGreen);
    pressure3->setColor(Qt::blue);
    pressure9->setColor(Qt::blue);
    pressure4->setColor(Qt::darkBlue);
    pressure10->setColor(Qt::darkBlue);
    pressure5->setColor(Qt::cyan);
    pressure11->setColor(Qt::cyan);
    pressure6->setColor(Qt::magenta);
}

void MainWindow::charpointupdate(){
    // 添加新数据点
    pressure1->append(time_tick, pressure[0]);
    pressure2->append(time_tick, pressure[1]);
    pressure3->append(time_tick, pressure[2]);
    pressure4->append(time_tick, pressure[3]);
    pressure5->append(time_tick, pressure[4]);
    pressure6->append(time_tick, pressure[5]);
    pressure7->append(time_tick, pressure[6]);
    pressure8->append(time_tick, pressure[7]);
    pressure9->append(time_tick, pressure[8]);
    pressure10->append(time_tick, pressure[9]);
    pressure11->append(time_tick, pressure[10]);

    // 检查并更新 x 轴范围
    if(time_tick > xrange) {
        pressure1X.setRange(time_tick - xrange, time_tick);

        // 定义一个 lambda 函数来清理旧数据
        auto removeOldData = [this](QSplineSeries* series) {
            int removeCount = 0;
            while (removeCount < series->count() && series->at(removeCount).x() < (time_tick - xrange)) {
                ++removeCount;
            }
            if (removeCount > 0) {
                series->removePoints(0, removeCount);
            }
        };

        // 清理每个压力系列的旧数据
        removeOldData(pressure1);
        removeOldData(pressure2);
        removeOldData(pressure3);
        removeOldData(pressure4);
        removeOldData(pressure5);
        removeOldData(pressure6);
        removeOldData(pressure7);
        removeOldData(pressure8);
        removeOldData(pressure9);
        removeOldData(pressure10);
        removeOldData(pressure11);
    }

    // 增加时间刻度
//    time_tick = (time_tick + 1) % 50000;
    ++time_tick;
    if(time_tick % 10000 == 0 && comflag == 1){
        serial->close();
        comflag = 0;
        serialopen();
        qDebug() << "reset success";
    }
}


void MainWindow::reset(){
    ui->finger1->setValue(0);
    ui->finger2->setValue(0);
    ui->finger3->setValue(0);
    ui->finger4->setValue(0);
    ui->finger5->setValue(0);
    ui->damuzhi->setValue(800);
    ui->sizhi->setValue(1000);
}

void MainWindow::onSliderMoved(int value) {
    QSlider* senderSlider = qobject_cast<QSlider*>(sender());
    if (senderSlider == nullptr) return;
    if (    (senderSlider == ui->finger1 && ui->checkBox_1->isChecked()) ||
            (senderSlider == ui->finger2 && ui->checkBox_2->isChecked()) ||
            (senderSlider == ui->finger3 && ui->checkBox_3->isChecked()) ||
            (senderSlider == ui->finger4 && ui->checkBox_4->isChecked()) ||
            (senderSlider == ui->finger5 && ui->checkBox_5->isChecked())
            ) {
        if (ui->checkBox_1->isChecked()) {
            ui->finger1->setValue(value);
        }
        if (ui->checkBox_2->isChecked()) {
            ui->finger2->setValue(value);
        }
        if (ui->checkBox_3->isChecked()) {
            ui->finger3->setValue(value);
        }
        if (ui->checkBox_4->isChecked()) {
            ui->finger4->setValue(value);
        }
        if (ui->checkBox_5->isChecked()) {
            ui->finger5->setValue(value);
        }
    }

}

void MainWindow::setcanid(){
    uint8_t data[16];
    uint16_t pressureBoardId = static_cast<uint16_t>(ui->spinBox_3->value());
    uint16_t ctrlBoardId = static_cast<uint16_t>(ui->spinBox_4->value());
//    uint16_t pressureId = 65535 - boardId;
    if(comflag){
        qDebug() << "id setting";
        data[0] = 0xAA;
        data[1] = 0x00;
        data[2] = 0x00;
        data[3] = 0x08;

        data[4] = 0x00;
        data[5] = 0x00;
        data[6] = 0x00;
        data[7] = 0xFF;

        data[8] = 0x00;
        data[9] = (pressureBoardId >> 8);
        data[10] = pressureBoardId & 0xFF;
        data[11] = 0x00;

        data[12] = 0x00;
        data[13] = 0x00;
        data[14] = 0x00;
        data[15] = 0x00;
        serial->write(reinterpret_cast<char*>(data), sizeof(data));

        data[0] = 0xAA;
        data[1] = 0x00;
        data[2] = 0x00;
        data[3] = 0x08;

        data[4] = 0x00;
        data[5] = 0x00;
        data[6] = 0x00;
        data[7] = 0x00;

        data[8] = 0x00;
        data[9] = (ctrlBoardId >> 8);
        data[10] = ctrlBoardId & 0xFF;
        data[11] = 0x00;

        data[12] = 0x00;
        data[13] = 0x00;
        data[14] = 0x00;
        data[15] = 0x00;
        serial->write(reinterpret_cast<char*>(data), sizeof(data));
    }
}

void MainWindow::setid(){
    idsetflag = 1;
}

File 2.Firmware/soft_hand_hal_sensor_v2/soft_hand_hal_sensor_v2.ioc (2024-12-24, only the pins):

Mcu.UserName=STM32F103VETx
PA1.Signal=ADCx_IN1
PA10.Signal=USART1_RX
PA11.Signal=CAN_RX
PA12.Signal=CAN_TX
PA13.Signal=SYS_JTMS-SWDIO
PA14.Signal=SYS_JTCK-SWCLK
PA2.Signal=ADCx_IN2
PA3.Signal=ADCx_IN3
PA4.Signal=ADCx_IN4
PA5.Signal=ADCx_IN5
PA6.Signal=ADCx_IN6
PA7.Signal=ADCx_IN7
PA9.Signal=USART1_TX
PB0.Signal=ADCx_IN8
PB1.Signal=ADCx_IN9
PC0.Signal=ADCx_IN10
PC1.Signal=ADCx_IN11
PC2.Signal=ADCx_IN12

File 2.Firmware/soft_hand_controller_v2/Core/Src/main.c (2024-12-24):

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
/* Includes ------------------------------------------------------------------*/
#include "main.h"
#include "can.h"
#include "tim.h"
#include "gpio.h"


/* USER CODE BEGIN PV */
CAN_RxHeaderTypeDef RxHeader;
uint8_t RxData[8];

/* USER CODE END PV */

void SystemClock_Config(void);
/**
  * @brief  The application entry point.
  * @retval int
  */
int main(void)
{

  /* MCU Configuration--------------------------------------------------------*/

  /* Reset of all peripherals, Initializes the Flash interface and the Systick. */
  HAL_Init();

  /* Configure the system clock */
  SystemClock_Config();

  /* Initialize all configured peripherals */
  MX_GPIO_Init();
  MX_CAN_Init();
  MX_TIM2_Init();
  MX_TIM3_Init();
  MX_TIM4_Init();
  /* USER CODE BEGIN 2 */
    __HAL_AFIO_REMAP_TIM3_PARTIAL(); // Remap
    CAN_Init();
    HAL_TIM_PWM_Start(&htim2, TIM_CHANNEL_2);
    HAL_TIM_PWM_Start(&htim3, TIM_CHANNEL_1);
    HAL_TIM_PWM_Start(&htim3, TIM_CHANNEL_2);
    HAL_TIM_PWM_Start(&htim4, TIM_CHANNEL_1);
    HAL_TIM_PWM_Start(&htim4, TIM_CHANNEL_2);
    HAL_TIM_PWM_Start(&htim4, TIM_CHANNEL_3);
    HAL_TIM_PWM_Start(&htim4, TIM_CHANNEL_4);
    HAL_TIM_PWM_Start(&htim2, TIM_CHANNEL_1);
    //    __HAL_TIM_SetCompare(&htim3, TIM_CHANNEL_2, 1000);
    //    PWM_SetCompare(0, 1000);
    // HAL_CAN_ActivateNotification(&hcan, CAN_IT_RX_FIFO0_MSG_PENDING);
    //    __HAL_CAN_ENABLE_IT(&hcan, CAN_IT_RX_FIFO0_MSG_PENDING);

  /* USER CODE END 2 */

  /* Infinite loop */
  /* USER CODE BEGIN WHILE */
//    HAL_UART_Transmit(&huart1, "init", 4, 5);
    while (1)
    {
        if (HAL_CAN_GetRxFifoFillLevel(&hcan, CAN_RX_FIFO0) != 1)
        {
        }
        if (HAL_CAN_GetRxMessage(&hcan, CAN_RX_FIFO0, &RxHeader, RxData) == HAL_OK)
        {

            switch (RxHeader.FilterMatchIndex)
            {
            case 0: /*广播*/
#ifdef TEST_MODE
                HAL_UART_Transmit(&huart1, "Bank0Recived", 12, 5);
#endif
                FILTER_MsgProcess(RxData);
                break;
            case 1:
#ifdef TEST_MODE
                HAL_UART_Transmit(&huart1, "Bank1Recived", 12, 5);
#endif
                SERVO_MsgProcess(RxData);
                break;
            }
        }
//        HAL_Delay(5);
    /* USER CODE END WHILE */

    /* USER CODE BEGIN 3 */
    }
  /* USER CODE END 3 */
}

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


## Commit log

2024-11-13 增加了v1.3.0上位机源代码
2024-11-22 升级上位机版本: 1.3.0 -> 2.0.0
2024-12-24 [Readme][Model][Hw][Fw][Sw][Docs] add
    [makeProjectedPlanarWire.x_t, 中指机架.STL, 中指机架_L.STL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]

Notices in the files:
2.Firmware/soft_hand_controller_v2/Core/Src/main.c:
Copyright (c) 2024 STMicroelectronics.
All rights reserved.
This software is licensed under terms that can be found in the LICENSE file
